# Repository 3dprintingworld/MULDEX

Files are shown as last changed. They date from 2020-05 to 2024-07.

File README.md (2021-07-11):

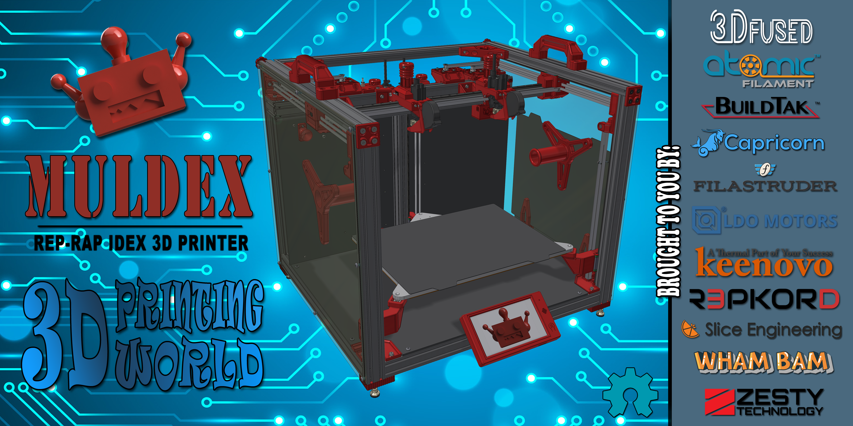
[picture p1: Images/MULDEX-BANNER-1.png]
Muldex


# Muldex
Opensource IDEX REP-RAP 3D Printer
### Print Volume:
Single Mode: 340mm x 300mm x 300mm<br/>
Copy Mode: 190mm x 300mm x 300mm<br/>
Dual Extruder: 310mm x 300mm x 300mm
### Build Platform:<br/>
300mm X 400mm <br/>
120v Silicone heater <br/>
8mm Mic 6 Aluminum Plate<br/>
Kinematic Coupled Bed<br/>
Independent motor leveled bed<br/>
Flex Plate System<br/>
### Kinematics:<br/>
X-Y-U Axis: Dual Markforged <br/>
Z-Axis: Belted 8mm Planetary Steppers<br/>
12 and 9mm Sq. Rail Bearings<br/>
Controller: Duet 2/Panel Due i7/Duex 5/Filament Monitors<br/>
Frame: 4020 & 2020 Extruded Aluminum<br/>
### Componets:<br/>
Independently Adjustable Nozzle Height - Slice Engineering Copperhead Hotend <br/>
Direct Drive Bondtech BMG Extruder or Remote Direct Drive Zesty Nimble Extruder <br/>
Purge Bucket/Ooze guards<br/>
Reverse Bowden w/filament runout<br/>
Bludex

### Links:
Facebook: [Muldex User Group](https://www.facebook.com/groups/961386687613469)<br/>
BMG Extruder Carriage Render: [Animation](https://https://youtu.be/zeYfmW2Gefs)<br/>
<br/>
Community Updates:<br/>
[ Guillaume's Drilling Jigs](https://www.prusaprinters.org/prints/32532-drilling-jigs-for-2020-and-2040-extrusions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)<br/>
[Guillame's Slim Fan Modules](https://www.prusaprinters.org/prints/57909-slim-fan-modules-for-muldex-3d-printer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)<br/>
[Guillame's Cable Duct](https://www.prusaprinters.org/prints/59193-industrial-style-cable-ducts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)<br/>
<br/>
### Kits from LDO are Available!!
Motor, rail, bolt, frame, and bed kits from LDO can be found [here](https://dddprintingworld.com/collections/mulex)<br/>
Custom cut Mic6 bed from [3Dfused ](https://3dfused.com/product/muldex-by-3dprinting-world-bed/)<br/>
Pannel Kit from [Repkord](https://www.repkord.com/products/sidepanel-set-for-muldex)<br/>
Additional links can be found in the bom. <br/>

### Sponsers:
[3D Fused](https://www.3dfused.com)<br/>
[Atomic Filament](https://www.atomicfilament.com)<br/>
[Buildtak](https://www.buildtak.com)<br/>
[Capricorn](https://www.captubes.com)<br/>
[Filastruder](https://www.filastruder.com)<br/>
[LDO Motors](https://www.ldomotors.com)<br/>
[Keenovo](https://keenovo.store/.com)<br/>
[Repkord](https://www.repkord.com)<br/>
[Slice Engineering](https://www.sliceengineering.com)<br/>
[Wham Bam](https://www.whambamsystems.com)<br/>
[Zesty Tech](https://zesty.tech/)<br/>

### Firmware, to do list:<br/>
1. Tool select Macros<br/>
2. Add macros to turn off mesh bed and change first layer heights<br/>
3. Mirror mode support<br/>

Note: current firmware only supports the BMG extruder, X-axis on left.<br/>
  
### Wiring
Wiring

### KINEMATICS
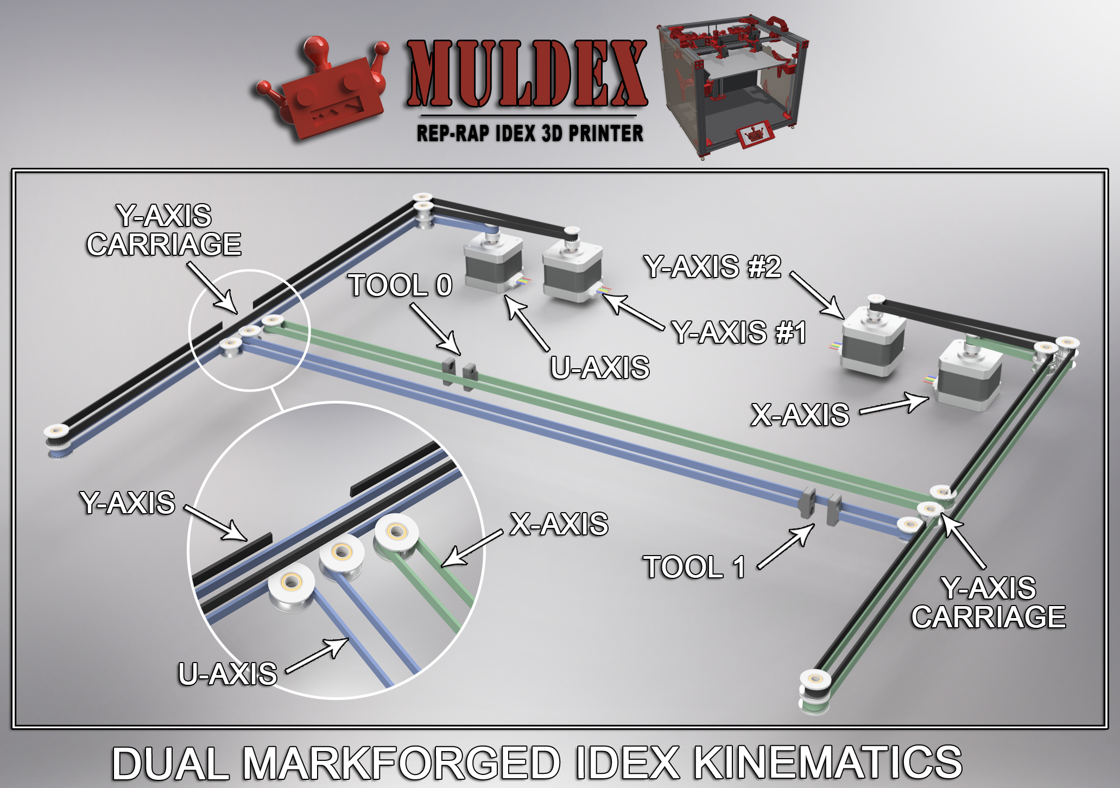
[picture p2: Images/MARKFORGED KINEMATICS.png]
Belt


### Print Examples
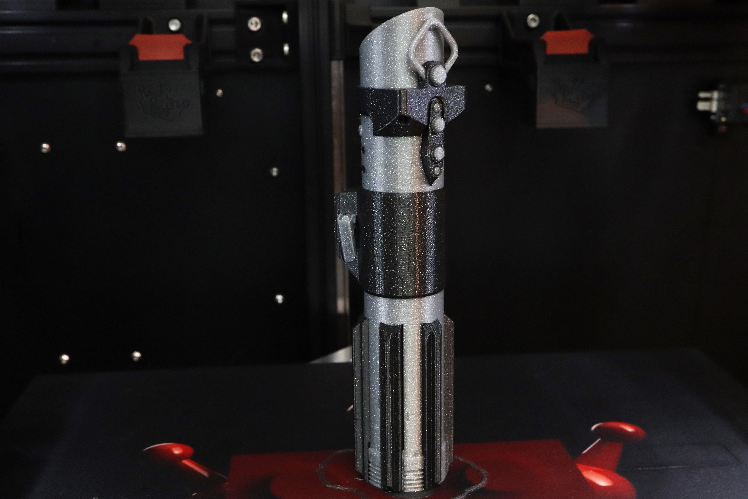
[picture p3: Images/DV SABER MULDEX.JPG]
Saber

Bull

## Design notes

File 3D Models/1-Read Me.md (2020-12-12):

Notice: Step files are prelimary and for reference only. For the most up to date models use the stl files.

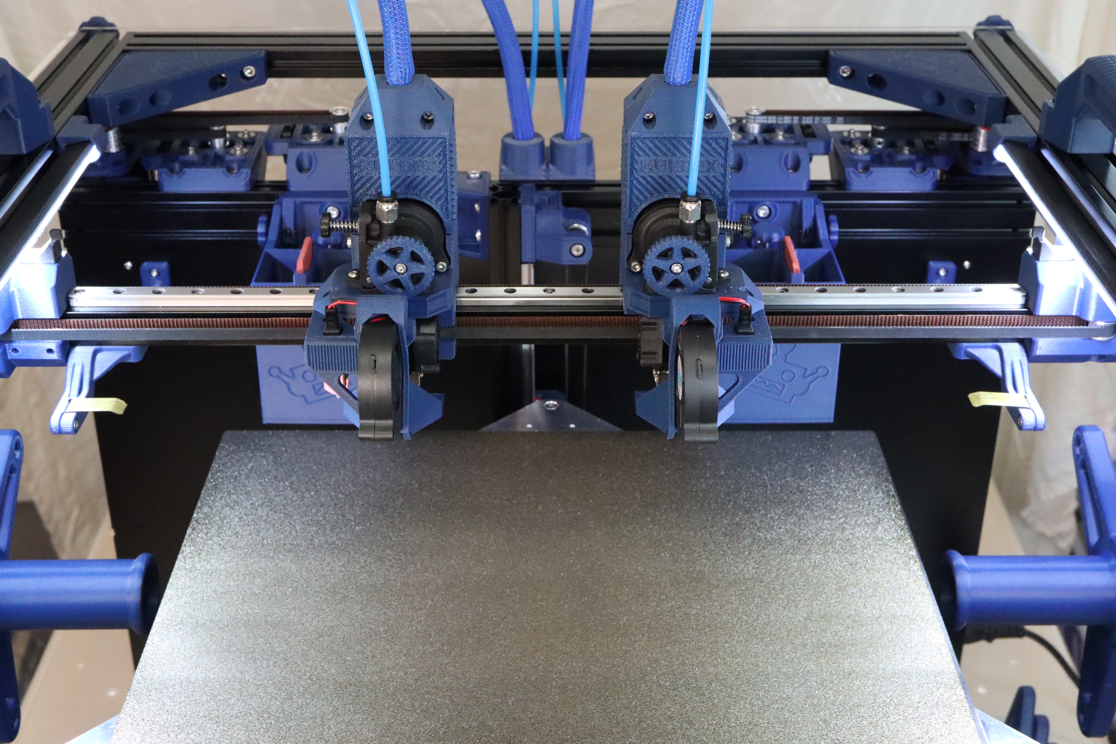
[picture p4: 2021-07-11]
Images/MULDEX-9.JPG

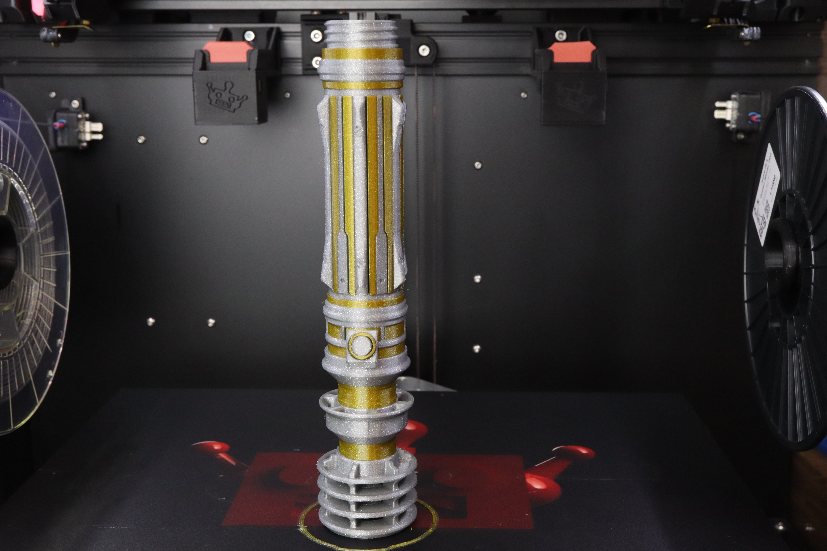
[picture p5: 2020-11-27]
Images/LEIA 1.JPG

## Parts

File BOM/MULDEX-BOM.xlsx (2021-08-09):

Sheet: COMPONENTS
2021-05-29 |  |  | BOM | TOTAL COST: | $2494.22 | (REF ONLY, CONTAINS OPTIONS)
QTY | Part Number | Description | Vendor | Thumbnail | UNIT | EACH | TOTAL | Notes:
1 | MULDEX-19-01 | BED PLATE | 3DFUSED (https://3dfused.com/product/muldex-by-3dprinting-world-bed/) |  | 1 | $135.00 | $135.00 | LDO ALTERATIVE (https://www.dddprintingworld.com/products/muldex-bed)
1 | MULDEX-11-02 | OOZE GUARD, X-AXIS | 3DPW |  |  |  | $0.00
1 | MULDEX-11-03 | OOZE GUARD, X-AXIS | 3DPW |  |  |  | $0.00
3 | 10MM X M4 | BALL END | ALIEXPRESS |  | 1 | $2.18 | $2.18
1 | 120C | THERMO FUSE | AMAZON (https://amzn.to/3wICdZ6) |  | 1 | $12.50 | $12.50
2 | JST-SM MALE | CONNECTOR | AMAZON (https://amzn.to/3oZNOjU) |  | 1 | $8.00 | $8.00
1 |  | WIRELESS MICROSCOPE | AMAZON (https://amzn.to/2XF4dyd) |  | 1 | $42.99 | $42.99 | OPTIONAL, FOR NOZZLE ALIGNMENT
3 | PETG | 1KG PETG CARBON FIBER | ATOMIC (https://atomicfilament.com/collections/petg-3d-printer-filament-us-made-with-free-shipping/products/carbon-fiber-black-petg-pro) |  | 3 | $49.99 | $149.97 | REQUIRES JUST OVER 2 KG
1 | BTFS300X400 | FLEX PLATE SYSTEM | BUILDTAK (https://www.buildtak.com/) |  | 1 | $140 | $140.00 | LDO POWER COATED ALTERATIVE $60.00 (https://www.dddprintingworld.com/products/powder-coated-pei-flex-plate)
2 | 1M LG | TL BOWDEN TUBING | CAPRICORN (https://www.captubes.com/shop/) |  | 2 | $11.99 | $23.98
2 | 4MM ID X 2MM ID 43.5MM LG | XS BOWDEN TUBING | CAPRICORN (https://www.captubes.com/shop/) |  | 1 | $11.99 | $11.99
1 | 5630 | LED STRIP W/EXTRUDED COVER 24V, DBL ROW | EBAY (https://www.ebay.com/itm/12V-24V-LED-5730-Strip-Light-Tube-Bar-Hard-Rigid-Lamp-White-For-Car-Showcase-USA/283971163922) |  | 2 | $3.81 | $7.62
16 | 5MM DIA X 3MM LG. | NEODYMIUM MAGNET | EBAY (https://www.ebay.com/itm/333227744234?var=542240236420) |  | 1 | $12.00 | $12.00
4 | 1.75 | E3D BOWDEN COUPLING, FOR PLASTIC | FILASTRUDER (https://www.filastruder.com/products/bowden-couplings-all-types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) |  | 2 | $2.99 | $5.98
4 | 2GT-16T-6-D | GATES DRIVE PULLEY, 16 TOOTH X 6MM WIDE | FILASTRUDER (https://www.filastruder.com/products/gates-2gt-pulley?_pos=1&_sid=b7f8e2fd2&_ss=r) |  | 4 | $4.99 | $19.96
10 | 2GT-20T-6-I | GATES IDLER PULLEY, 5MM BORE 20 TOOTH, 6MM WIDE | FILASTRUDER (https://www.filastruder.com/products/gates-2gt-idler?_pos=1&_sid=3b1905a2a&_ss=r) |  | 10 | $6.99 | $69.90
8 | 2GT-20T-6-SI | GATES IDLER PULLEY, 5MM BORE 20 SMOOTH, 6MM WIDE | FILASTRUDER (https://www.filastruder.com/products/gates-2gt-idler?_pos=1&_sid=3b1905a2a&_ss=r) |  | 8 | $7.49 | $59.92
3 | 2GT-20T-9-D | GATES DRIVE PULLEY, 20 TOOTH X 9MM WIDE | FILASTRUDER (https://www.filastruder.com/products/gates-2gt-pulley?_pos=1&_sid=b7f8e2fd2&_ss=r) |  | 3 | $5.99 | $17.97 | Requires the ID to be bored to 8mm. Consider Amazon or Aliexpress for 8mm bore. (https://amzn.to/3r480R3)
3 | 2GT-20T-9-I | GATES IDLER PULLEY, 5MM BORE 20 TOOTH, 9MM WIDE | FILASTRUDER (https://www.filastruder.com/products/gates-2gt-idler?_pos=1&_sid=3b1905a2a&_ss=r) |  | 3 | $6.99 | $20.97
18 | 5MM ID X 6MM OD X .4MM | BEARING SPACER | FILASTRUDER (https://www.filastruder.com/collections/railcore/products/shims-for-shoulder-screws?variant=17989593104455) |  | 1 | $9.99 | $9.99
2 | 6MM X 1290MM LG 2580 | GATES 2GT TIMING BELT | FILASTRUDER (https://www.filastruder.com/products/gates-2gt-belts?_pos=2&_sid=c064cd569&_ss=r) |  | 2 | $12.77 | $25.54
2 | 6MM X 2270MM LG | GATES 2GT TIMING BELT | FILASTRUDER (https://www.filastruder.com/products/gates-2gt-belts?_pos=2&_sid=c064cd569&_ss=r) |  | 2 | $22.47 | $44.94
1 | 7i | DUET 3D, PANELDUE | FILASTRUDER (https://www.filastruder.com/collections/electronics/products/paneldue-7i) |  | 1 | $99.99 | $99.99
3 | 9MM X 855MM LG. | GATES 2GT TIMING BELT | FILASTRUDER (https://www.filastruder.com/products/gates-2gt-belts?_pos=2&_sid=c064cd569&_ss=r) |  | 3 | $12.74 | $38.22
1 | AQA211VL | SSR | FILASTRUDER (https://www.filastruder.com/products/solid-state-relay?_pos=2&_sid=b83730b5f&_ss=r) |  | 1 | $21.99 | $21.99
1 | BL-TOUCH | LEVELING SENSOR | FILASTRUDER (https://www.filastruder.com/products/bltouch-automatic-bed-leveling-probe?_pos=4&_sid=87edbc376&_ss=r) |  | 1 | $34.99 | $34.99
1 | DUET 2 WIFI | DUET 3D, MAIN BOARD | FILASTRUDER (https://www.filastruder.com/collections/electronics/products/duet-wifi) |  | 1 | $169.99 | $169.99
1 | DUEX 5 | DUET 3D, EXPANSION BOARD | FILASTRUDER (https://www.filastruder.com/collections/electronics/products/duex2-and-duex-5-expansion-board) |  | 1 | $74.99 | $74.99
2 | FILAMENT SENSOR | DUET 3D, MAGNETIC TYPE | FILASTRUDER (https://www.filastruder.com/collections/electronics/products/duet-magnetic-filament-monitor) |  | 2 | $54.99 | $109.98 | OPTIONAL
3 | MGN12H x 370mm LG. G=10mm | LDO LINEAR RAIL, W/1 BEARING | FILASTRUDER (https://www.filastruder.com/products/ldo-linear-rails?variant=32433716265031) |  | 3 | $20.00 | $60.00 | INCLUDED IN LDO RAIL KIT
2 | MGN12H x 420mm lg. G=10mm | LDO LINEAR RAIL,, W/1 BEARING | FILASTRUDER (https://www.filastruder.com/products/ldo-linear-rails?variant=32433716265031) |  | 2 | $25.00 | $50.00 | INCLUDED IN LDO RAIL KIT
1 | MGN9H x 490mm lg. G=5mm | LDO LINEAR RAIL, W/2 BEARINGS | FILASTRUDER (https://www.filastruder.com/products/ldo-linear-rails?variant=32433716265031) |  | 1 | $35.00 | $35.00 | INCLUDED IN LDO RAIL KIT
1 | SM-DU-100 | BLTOUCH - 1 M CABLE | FILASTRUDER (https://www.filastruder.com/products/bltouch-1000mm-cable?_pos=1&_sid=87edbc376&_ss=r) |  | 1 | $2.99 | $2.99
1 | SILICONE | SILICONE HEATING PAD, 400X300 | KEENOVO (https://keenovo.store/products/keenovo-standard-rectangle-silicone-heater-3d-printer-build-plate-heatbed-heating-pad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) |  | 1 | $86.50 | $86.50
2 | 42STH25-1004AC | 1.8 SLIM POWER STEPPER | LDO (https://www.dddprintingworld.com/products/muldex-motor-kit) |  | 2 | $16 | $32.00 | INCLUDED IN LDO MOTOR KIT
4 | 42STH40-100AC | STEPPER MOTOR | LDO (https://www.dddprintingworld.com/products/muldex-motor-kit) |  | 4 | $16 | $64.00 | INCLUDED IN LDO MOTOR KIT
1 | LH-MIRRORED | ORBITER EXTRUDER | LDO (https://lukeslabonline.com/products/orbiter-v-1-5) |  | 1 | $55.00 | $55.00 | MJF PRINT MIRRORED HOUSING AND LEVERL
2 | OPTICAL | ENDSTOP SWITCH | HONG (https://www.amazon.com/gp/product/B071KBC3P8?linkId=593f3d3ddd48f557f777a21beb5f8118&language=en_US) |  | 1 | $9.96 | $9.96
1 | RH - STANDARD | ORBITER EXTRUDER | LDO (https://lukeslabonline.com/products/orbiter-v-1-5) |  | 1 | $55.00 | $55.00
1 | TOOL BOARD | DUMB BOARD, MULDEX ADDITION | LUKES LAB (https://lukeslabonline.com/products/dumbboard-muldex) |  | 2 | $15.00 | $30.00
3 | 1462N24 | SILICONE 1/8" X 3/4" CUT TO 1-3/4" LG. | MCMASTER (https://www.mcmaster.com/1462N24/) |  | 1 | $8.13 | $8.13 | OPTIONAL FOR WIPE
3 | 5862K124 | MAGNET, N52 1/2" DIA. X 3/8" THICK | MCMASTER (https://www.mcmaster.com/5862K124/) |  | 3 | $3.58 | $10.74
5 | 6301K780 | LEVELING FOOT, 6MM | MCMASTER (https://www.mcmaster.com/6301K78/) |  | 5 | $5.60 | $28.00 | OPTIONAL
4 | 92273A003 | GARLITE SPACER, .115"ID X .188" OD X.188" LG | MCMASTER (https://www.mcmaster.com/92273A003/) |  | 1 | $1.31 | $1.31 | OPTIONAL, BOWDEN TUBE WOULD ALSO WORK
1 | LRS-350-24 | MEANWELL POWER SUPPLY | MEANWELL (https://www.amazon.com/gp/product/B07SQLJG5L?linkId=c7ae342bb727b12a6109943f33807af6&language=en_US) |  | 1 | $32.20 | $32.20
2 | ZD-0026 | HORZONTAL LIMIT SWITCH | REIFENG (https://amzn.to/3cHwI2D) |  | 1 | $9.99 | $9.99 | OPTIONAL, ENDSTOPLESS HOMING FOR THE Y-AXIS
1 | MULDEX-00-01 | BACK COVER PANNEL | REPKORD (https://www.repkord.com/products/sidepanel-set-for-muldex) |  | 1 | $25.00 | $25.00
1 | MULDEX-03-03 | BACK PANNEL | REPKORD (https://www.repkord.com/products/sidepanel-set-for-muldex) |  | 1 | $25.00 | $25.00
1 | MULDEX-31-01 | SIDE PANEL | REPKORD (https://www.repkord.com/products/sidepanel-set-for-muldex) |  | 1 | $25.00 | $25.00
1 | MULDEX-31-02 | SIDE PANEL, IEC | REPKORD (https://www.repkord.com/products/sidepanel-set-for-muldex) |  | 1 | $25.00 | $25.00
1 | MULDEX-32-01 | BOTTOM PANNEL | REPKORD (https://www.repkord.com/products/sidepanel-set-for-muldex) |  | 1 | $25.00 | $25.00
1 | 4304.6072 | IEC INLET C14 W/SWITCH | SCHURTER (https://www.digikey.com/en/products/detail/schurter-inc/4304-6072/2645660) |  | 1 | $9.00 | $9.00
2 | .4MM | VANADUM NOZZLE | SLICE (https://www.sliceengineering.com/products/copperhead%E2%84%A2) |  | 2 | $34.99 | $69.98
2 | 25X25X10 | 24V DC FAN | SLICE (https://www.sliceengineering.com/products/copperhead%E2%84%A2) |  | 2 | $6.99 | $13.98
2 | COPPERHEAD-1 | HEAT BREAK, STANDARD VARIANT | SLICE (https://www.sliceengineering.com/products/copperhead%E2%84%A2) |  | 2 | $29.99 | $59.98
2 | COPPERHEAD-2 | HOT BLOCK | SLICE (https://www.sliceengineering.com/products/copperhead%E2%84%A2) |  | 2 | $24.99 | $49.98
2 | COPPERHEAD-3 | HEAT SINK,SCREW MOUNT | SLICE (https://www.sliceengineering.com/products/copperhead%E2%84%A2) |  | 2 | $44.99 | $89.98
2 | COPPERHEAD-4 | HIGH TEMP THERMISTER | SLICE (https://www.sliceengineering.com/collections/accessories/products/thermistor-high-temperature) |  | 2 | $39.99 | $79.98
2 | COPPERHEAD-5 | 24V, HEATER CARTRIAGE | SLICE (https://www.sliceengineering.com/collections/accessories/products/50w-heater-cartridge?variant=29760199196744) |  | 2 | $19.99 | $39.98
2 | 5015 | BLOWER, 24VDC | SOUND ORIGINAL (https://amzn.to/2XFXwvH) |  | 1 | $13.99 | $13.99
1 | MULDEX-19-03 | FLEX PLATE | WHAM BAM |  |  |  | $0.00

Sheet: EXTRUSIONS
2021-05-29 |  |  | BOM | TOTAL COST: | $184.00 | (REF ONLY, CONTAINS OPTIONS)
QTY | Part Number | Description | Vendor | Thumbnail | UNIT | EACH | TOTAL | Notes:
1 | MULDEX-01-09 | EXTRUSION, Z-AXIS | LDO (https://www.dddprintingworld.com/products/ldo-frame-kit) |  | 1 | $7.00 | $7.00 | ALTERATIVE MISUMI PN: HFSB5-2040-455 INCLUDED IN LDO FRAME KIT
1 | MULDEX-01-10 | EXTRUSION, MOTOR MOUNT | LDO (https://www.dddprintingworld.com/products/ldo-frame-kit) |  | 1 | $9.00 | $9.00 | ALTERATIVE MISUMI PN: HFSB5-2040-635
2 | MULDEX-02-01 | EXTRUSIOIN, Y-AXIS | LDO (https://www.dddprintingworld.com/products/ldo-frame-kit) |  | 2 | $9.00 | $18.00 | ALTERATIVE MISUMI PN: HFSB5-2040-555 INCLUDED IN LDO FRAME KIT
2 | MULDEX-02-02 | EXTRUSION, STANDOFF | LDO (https://www.dddprintingworld.com/products/fastener-kit) |  | 2 | $6.00 | $12.00 | ALTERATIVE MISUMI PN: HFSB5-2040-60-SC INCLUDED IN LDO FRAME KIT
2 | MULDEX-02-03 | EXTRUSION, FRONT VERTICAL | LDO (https://www.dddprintingworld.com/products/ldo-frame-kit) |  | 2 | $12.00 | $24.00 | ALTERATIVE MISUMI PN: HFSB5-2040-505-SC INCLUDED IN LDO FRAME KIT
2 | MULDEX-02-04 | EXTRUSION, BACK VERTICAL | LDO (https://www.dddprintingworld.com/products/ldo-frame-kit) |  | 2 | $15.00 | $30.00 | ALTERATIVE MISUMI PN: HFSB5-2040-505-SC INCLUDED IN LDO FRAME KIT
1 | MULDEX-02-05 | EXTRUSION, BACK SUPPORT | LDO (https://www.dddprintingworld.com/products/ldo-frame-kit) |  | 1 | $12.00 | $12.00 | ALTERATIVE MISUMI PN: HFSB5-2020-555-SC INCLUDED IN LDO FRAME KIT
2 | MULDEX-02-06 | EXTRUSION, FRONT BOTTOM | LDO (https://www.dddprintingworld.com/products/ldo-frame-kit) |  | 2 | $14.00 | $28.00 | ALTERATIVE MISUMI PN: HFSB5-2040-555-SC INCLUDED IN LDO FRAME KIT
2 | MULDEX-02-07 | EXTRUSION, BOTTOM SIDES | LDO (https://www.dddprintingworld.com/products/ldo-frame-kit) |  | 2 | $14.00 | $28.00 | ALTERATIVE MISUMI PN: HFSB5-2040-515-SC INCLUDED IN LDO FRAME KIT
1 | MULDEX-02-08 | EXTRUSION, BACK | LDO (https://www.dddprintingworld.com/products/ldo-frame-kit) |  | 1 | $16.00 | $16.00 | ALTERATIVE MISUMI PN: HFSB5-2040-595-SC INCLUDED IN LDO FRAME KIT

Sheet: FASTENERS
2021-05-29 |  |  | BOM | TOTAL COST: | $88.69 | (REF ONLY, CONTAINS OPTIONS)
QTY | Part Number | Description | Vendor | Thumbnail | UNIT | EACH | TOTAL | Notes:
2 | M4x0.7 x 35 | SHCS |  |  | 1 |  | $0.00 | INCLUDED IN LDO FASTENER KIT
4 | M2.5x0.45 x 10 | SHCS |  |  | 1 |  | $0.00 | INCLUDED IN LDO FASTENER KIT
4 | M2.5x0.45 x 12 | SHCS |  |  | 1 |  | $0.00 | INCLUDED IN LDO FASTENER KIT
16 | M3 | WASHER |  |  | 1 |  | $0.00 | INCLUDED IN LDO FASTENER KIT
50 | M3 x 0.5 | Hex Nut |  |  | 1 |  | $0.00 | INCLUDED IN LDO FASTENER KIT
17 | M3 x 0.5 x 10 | BHCS | https://www.dddprintingworld.com/products/fastener-kit |  | 1 |  | $0.00 | INCLUDED IN LDO FASTENER KIT
4 | M3 x 0.5 x 16 | BHCS |  |  | 1 |  | $0.00 | INCLUDED IN LDO FASTENER KIT
6 | M3 x 0.5 x 20 | HHCS |  |  | 1 |  | $0.00 | INCLUDED IN LDO FASTENER KIT
35 | M3x0.5 x 10 | SHCS |  |  | 1 |  | $0.00 | INCLUDED IN LDO FASTENER KIT
30 | M3x0.5 x 12 | SHCS |  |  | 1 |  | $0.00 | INCLUDED IN LDO FASTENER KIT
31 | M3x0.5 x 16 | SHCS |  |  | 1 |  | $0.00 | INCLUDED IN LDO FASTENER KIT
10 | M3x0.5 x 20 | SHCS |  |  | 1 |  | $0.00 | INCLUDED IN LDO FASTENER KIT
8 | M3x0.5 x 25 | SHCS |  |  | 1 |  | $0.00 | INCLUDED IN LDO FASTENER KIT
2 | M3x0.5 x 30 | SHCS |  |  | 1 |  | $0.00 | INCLUDED IN LDO FASTENER KIT
8 | M3x0.5 x 6 | SHCS |  |  | 1 |  | $0.00 | INCLUDED IN LDO FASTENER KIT
63 | M3x0.5 x 8 | SHCS |  |  | 1 |  | $0.00 | INCLUDED IN LDO FASTENER KIT
8 | M4 | Square Nut |  |  | 1 |  | $0.00 | INCLUDED IN LDO FASTENER KIT
16 | M4 x 0.7 | Hex Nut |  |  | 1 |  | $0.00 | INCLUDED IN LDO FASTENER KIT
10 | M4 x 0.7 x 12 | BHCS |  |  | 1 |  | $0.00 | INCLUDED IN LDO FASTENER KIT
4 | M4 x 0.7 x 8 | BHCS |  |  | 1 |  | $0.00 | INCLUDED IN LDO FASTENER KIT
3 | M4x12 | FHCS |  |  | 1 |  | $0.00 | INCLUDED IN LDO FASTENER KIT
6 | M5 x 0.8 | Hex Nut |  |  | 1 |  | $0.00 | INCLUDED IN LDO FASTENER KIT
22 | M5 x 0.8 x 10 | BHCS |  |  | 1 |  | $0.00 | INCLUDED IN LDO FASTENER KIT
2 | M5 x 0.8 x 16 | HHCS |  |  | 1 |  | $0.00 | INCLUDED IN LDO FASTENER KIT
6 | M5 x 0.8 x 16 | BHCS |  |  | 1 |  | $0.00 | INCLUDED IN LDO FASTENER KIT
43 | M5 x 0.8 x 8 | BHCS |  |  | 1 |  | $0.00 | INCLUDED IN LDO FASTENER KIT
75 | M5x0.8 x 10 | SHCS |  |  | 1 |  | $0.00 | INCLUDED IN LDO FASTENER KIT
12 | M5x0.8 x 12 | SHCS |  |  | 1 |  | $0.00 | INCLUDED IN LDO FASTENER KIT
52 | M5x0.8 x 16 | SHCS |  |  | 1 |  | $0.00 | INCLUDED IN LDO FASTENER KIT
19 | M5x0.8 x 20 | SHCS |  |  | 1 |  | $0.00 | INCLUDED IN LDO FASTENER KIT
2 | M5x0.8 x 25 | SHCS |  |  | 1 |  | $0.00 | INCLUDED IN LDO FASTENER KIT
8 | M5x12 | FHCS |  |  | 1 |  | $0.00 | INCLUDED IN LDO FASTENER KIT
51 | M3-20 SERIES | T-NUT, TWIST LOCK | AMAZON (https://amzn.to/2AKpMVb) |  | 1 |  | $0.00 | INCLUDED IN LDO FASTENER KIT
181 | M5-20 SERIES | T-NUT, TWIST LOCK | AMAZON (https://amzn.to/3gYKykv) |  | 2 |  | $0.00 | INCLUDED IN LDO FASTENER KIT
9 | M5 X 25MM LG. | S.S. SHOULDER BOLT | FILASTRUDER (https://www.filastruder.com/products/shoulder-screws-bolts?_pos=1&_sid=c289bef45&_ss=r&variant=17989593104455) |  | 9 | $1.99 | $17.91
6 | M5 X 30MM LG. | S.S. SHOULDER BOLT | FILASTRUDER (https://www.filastruder.com/products/shoulder-screws-bolts?_pos=1&_sid=c289bef45&_ss=r&variant=17989593104455) |  | 6 | $1.99 | $11.94
1 | FASTENER KIT | THE FASTERNERS MARKED INCLUDED IN THE NOTES COLUMN | LDO (https://www.dddprintingworld.com/products/fastener-kit) |  | 1 | $42.00 | $42.00
2 | 93625A100 | M3 NYLOCK | MCMASTER |  | 1 | $5.31 | $5.31 | OPTIONAL, STANDARD NUT WOULD WORK
5 | 94180A371 | HEAT SET INSERT, M6 | MCMASTER (https://www.mcmaster.com/catalog/126/3507) |  | 1 | 9.68 | $9.68 | OPTIONAL, FOR MOUNTING FOOT
41 | IUB-M3-1 | M3 HEAT SET INSERT, MINI | PEM (https://www.dddprintingworld.com/products/fastener-kit) |  | 41 | $0.04 | $1.84

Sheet: ASSEMBLIES
2021-05-29 |  |  | BOM | TOTAL COST: | $0.00 | (REF ONLY, CONTAINS OPTIONS)
QTY | Part Number | Description | Vendor | Thumbnail | UNIT | EACH | TOTAL | Notes:
1 | MULDEX-01 | FRAME ASSEMBLY | 3DPW |  |  |  | $0.00
1 | MULDEX-02 | FRAME SUB-ASSEMBLY | 3DPW |  |  |  | $0.00
1 | MULDEX-03 | BACK PANEL ASSEMBLY | 3DPW |  |  |  | $0.00
1 | MULDEX-04 | MNT FOOT, FRONT LEFT | 3DPW |  |  |  | $0.00
1 | MULDEX-05 | MNT FOOT, FRONT RIGHT | 3DPW |  |  |  | $0.00
1 | MULDEX-06 | MNT FOOT, BACK RIGHT | 3DPW |  |  |  | $0.00
1 | MULDEX-07 | MOUNTING FOOT, BACK LEFT | 3DPW |  |  |  | $0.00
1 | MULDEX-08 | MOUNTING FOOT, CENTER | 3DPW |  |  |  | $0.00
1 | MULDEX-10 | KINEMATIC ASSEMBLY | 3DPW |  |  |  | $0.00
1 | MULDEX-11 | X-AXIS ASSEMBLY | 3DPW |  |  |  | $0.00
1 | MULDEX-43 | X-AXIS CARRIAGE | 3DPW |  |  |  | $0.00
1 | MULDEX-44 | U-AXIS CARRIAGE | 3DPW |  |  |  | $0.00
2 | MULDEX-14 | Y-AXIS CARRIAGE | 3DPW |  |  |  | $0.00
1 | MULDEX-15 | Z-AXIS ASSEMBLY | 3DPW |  |  |  | $0.00
1 | MULDEX-16 | Z-AXIS BELT ASSY, 1 | 3DPW |  |  |  | $0.00
1 | MULDEX-17 | Z-AXIS BELT ASSY, 2 | 3DPW |  |  |  | $0.00
1 | MULDEX-18 | Z-AXIS BELT ASSY, 3 | 3DPW |  |  |  | $0.00
1 | MULDEX-19 | HEAT BED ASSEMBLY | 3DPW |  |  |  | $0.00
1 | MULDEX-20 | IDLE ASSEMBLY, LH | 3DPW |  |  |  | $0.00
1 | MULDEX-21 | IDLE ASSEMBLY, LH | 3DPW |  |  |  | $0.00
1 | MULDEX-22 | U-AXIS MOTOR ASSY | 3DPW |  |  |  | $0.00
1 | MULDEX-23 | X-AXIS MOTOR ASSY | 3DPW |  |  |  | $0.00
1 | MULDEX-24 | Y-AXIS MOTOR ASSY, LH | 3DPW |  |  |  | $0.00
1 | MULDEX-25 | Y-AXIS MOTOR ASSY, RH | 3DPW |  |  |  | $0.00
2 | MULDEX-27 | THUMB SCREW ASSEMBLY | 3DPW |  |  |  | $0.00
1 | MULDEX-28 | FLEX PLATE CADDY ASSY | 3DPW |  |  |  | $0.00
2 | MULDEX-29 | BOWDEN STRAIN RELIF ASSY | 3DPW |  |  |  | $0.00
1 | MULDEX-30 | PANNEL ASSY, LEFT | 3DPW |  |  |  | $0.00
1 | MULDEX-31 | PANNEL ASSEMBLY, RIGHT | 3DPW |  |  |  | $0.00
1 | MULDEX-32 | BOTTOM PANEL ASSY | 3DPW |  |  |  | $0.00
1 | MULDEX-33 | SCRAPER ASSEMBLY, U-AXIS | 3DPW |  |  |  | $0.00
1 | MULDEX-34 | SCRAPPER ASSY, X-AXIS | 3DPW |  |  |  | $0.00
1 | MULDEX-35 | DUET PANNEL | 3DPW |  |  |  | $0.00
2 | MULDEX-36 | LIGHT BAR ASSEMBLY | 3DPW |  |  |  | $0.00
1 | MULDEX-37 | Y-AXIS STOP, RH | 3DPW |  |  |  | $0.00
1 | MULDEX-38 | Y-AXIS STOP, LH | 3DPW |  |  |  | $0.00
1 | MULDEX-41 | IEC CONNECTOR ASSY - UL | 3DPW |  |  |  | $0.00

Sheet: PRINTED PARTS
2021-05-29 |  |  | BOM | TOTAL COST: | $0.00 | (REF ONLY, CONTAINS OPTIONS)
QTY | Part Number | Description | Vendor | Thumbnail | UNIT | EACH | TOTAL | Notes:
2 | MULDEX-11-09 | SWITCH TRIGGER | ATOMIC |  | 1 |  | $0.00
1 | MULBOT-34-01 | SCRAPPER, FRAME X-AXIS | ATOMIC |  | 1 |  | $0.00
2 | MULDEX-01-01 | FRAME CORNER GUSSET | ATOMIC |  | 1 |  | $0.00
8 | MULDEX-01-02 | BACK PLATE BRACKET | ATOMIC |  | 1 |  | $0.00
2 | MULDEX-01-03 | PANNEL SUPPORT | ATOMIC |  | 1 |  | $0.00
1 | MULDEX-01-04 | Z-AXIS RAIL SUPPORT | ATOMIC |  | 1 |  | $0.00
2 | MULDEX-01-05 | HANDLE | ATOMIC |  | 1 |  | $0.00
2 | MULDEX-01-06 | FRONT END CAP | ATOMIC |  | 1 |  | $0.00
1 | MULDEX-01-07 | ENDCAP COVER | ATOMIC |  | 1 |  | $0.00
1 | MULDEX-03-01 | BACK PLATE, STRAIN RELIF | ATOMIC |  | 1 |  | $0.00
2 | MULDEX-03-02 | SENSOR MOUNT | ATOMIC |  | 1 |  | $0.00 | Optional- for filament monitor
8 | MULDEX-03-04 | DUET SPACER | ATOMIC |  | 1 |  | $0.00
3 | MULDEX-03-05 | INLET GUIDE | ATOMIC |  | 1 |  | $0.00 | Optional-If no filament monitor
2 | MULDEX-03-06 | CABLE COVER, STRAIGHT | ATOMIC |  | 1 |  | $0.00
2 | MULDEX-03-07 | CABLE COVER, VERT SHORT | ATOMIC |  | 1 |  | $0.00
2 | MULDEX-03-08 | CABLE COVER, HORZ | ATOMIC |  | 1 |  | $0.00
1 | MULDEX-03-08 | WIRE CLIP | ATOMIC |  | 1 |  | $0.00
2 | MULDEX-03-09 | CABLE COVER, VERT LONG | ATOMIC |  | 1 |  | $0.00
1 | MULDEX-03-10 | CABLE DUCT, BOTTOM | ATOMIC |  | 1 |  | $0.00
1 | MULDEX-03-11 | CABLE DUCT, TOP | ATOMIC |  | 1 |  | $0.00
1 | MULDEX-03-12 | CABLE DUCT, STRAIGHT | ATOMIC |  | 1 |  | $0.00
1 | MULDEX-03-13 | BACK PLATE, STRAIN RELIEF | ATOMIC |  | 1 |  | $0.00
1 | MULDEX-04-01 | FOOT PAD, FRONT LEFT | ATOMIC |  | 1 |  | $0.00
1 | MULDEX-05-01 | FOOT PAD, FRONT RIGHT | ATOMIC |  | 1 |  | $0.00
1 | MULDEX-06-01 | FOOT PAD, BACK RIGHT | ATOMIC |  | 1 |  | $0.00
1 | MULDEX-07-01 | FOOT PAD, BACK LEFT | ATOMIC |  | 1 |  | $0.00
1 | MULDEX-08-01 | FOOT PAD, CENTER | ATOMIC |  | 1 |  | $0.00
1 | MULDEX-11-06 | OOZE BLOCK, RH | ATOMIC |  | 1 |  | $0.00 | OPTIONAL
1 | MULDEX-11-07 | OOZE BLOCK, LH | ATOMIC |  | 1 |  | $0.00 | OPTIONAL
4 | MULDEX-12-02 | BELT CLAMP | ATOMIC |  | 1 |  | $0.00
2 | MULDEX-14-01 | Y-AXIS, BASE BLOCK | ATOMIC |  | 1 |  | $0.00
2 | MULDEX-14-02 | Y-AXIS, CLAMP BLOCK | ATOMIC |  | 1 |  | $0.00
2 | MULDEX-14-03 | Y-AXIS BELT CLAMP | ATOMIC |  | 1 |  | $0.00
2 | MULDEX-16-01 | Z-AXIS MOTOR MOUNT, 1&3 | ATOMIC |  | 1 |  | $0.00
1 | MULDEX-16-02 | Z-AXIS COUPLING, 1 | ATOMIC |  | 1 |  | $0.00
1 | MULDEX-16-03 | Z-AXIS TAKEUP MOUNT, 1 | ATOMIC |  | 1 |  | $0.00
1 | MULDEX-16-04 | Z-AXIS TAKUP BRACKET, 1 | ATOMIC |  | 1 |  | $0.00
3 | MULDEX-16-05 | BELT CLAMP, Z | ATOMIC |  | 1 |  | $0.00
3 | MULDEX-16-06 | BELT CLAMP, Z | ATOMIC |  | 1 |  | $0.00
1 | MULDEX-17-02 | Z-AXIS TAKUP, 2 | ATOMIC |  | 1 |  | $0.00
1 | MULDEX-17-03 | Z-AXIS COUPLING, 2 | ATOMIC |  | 1 |  | $0.00
1 | MULDEX-17-04 | Z-AXIS MOTOR MOUNT, 2 | ATOMIC |  | 1 |  | $0.00
1 | MULDEX-17-05 | Z-AXIS TAKUP MOUNT, 2 | ATOMIC |  | 1 |  | $0.00
1 | MULDEX-18-02 | Z-AXIS COUPLING, 3 | ATOMIC |  | 1 |  | $0.00
1 | MULDEX-18-03 | Z-AXIS TAKUP MOUNT, 3 | ATOMIC |  | 1 |  | $0.00
1 | MULDEX-18-04 | Z-AXIS TAKEUP, 2 | ATOMIC |  | 1 |  | $0.00
1 | MULDEX-19-04 | STRAIN RELIEF | ATOMIC |  | 1 |  | $0.00
1 | MULDEX-20-01 | CORNER IDLER, RH | ATOMIC |  | 1 |  | $0.00
1 | MULDEX-21-01 | CORNER IDLER, LH | ATOMIC |  | 1 |  | $0.00
1 | MULDEX-22-01 | U-AXIS STEPPER MOUNT | ATOMIC |  | 1 |  | $0.00
4 | MULDEX-22-02 | TAKE UP KNOB | ATOMIC |  | 1 |  | $0.00
1 | MULDEX-23-01 | X-AXIS STEPPER MOUNT | ATOMIC |  | 1 |  | $0.00
1 | MULDEX-24-01 | Y-AXIS MOTOR MOUNT, LH | ATOMIC |  | 1 |  | $0.00
1 | MULDEX-25-01 | Y-AXIS MOTOR MOUNT, RH | ATOMIC |  | 1 |  | $0.00
2 | MULDEX-27-01 | THUMB KNOB, M5 HEX | ATOMIC |  | 1 |  | $0.00
2 | MULDEX-27-02 | THUMB KNOB COVER | ATOMIC |  | 1 |  | $0.00
2 | MULDEX-28-01 | FLEX PLATE CADDY | ATOMIC |  | 1 |  | $0.00 | OPTIONAL
2 | MULDEX-29-01 | REVERSE BOWDEN BRACKET | ATOMIC |  | 1 |  | $0.00
2 | MULDEX-29-03 | EXTRUDER CABLE, CLAMP | ATOMIC |  | 1 |  | $0.00
2 | MULDEX-29-04 | WIRE COMB | ATOMIC |  | 1 |  | $0.00
2 | MULDEX-30-02 | SPOOL HOLDER | ATOMIC |  | 1 |  | $0.00
1 | MULDEX-32-02 | FRONT BELT COVER, LH | ATOMIC |  | 1 |  | $0.00
1 | MULDEX-32-03 | FRONT BELT COVER, RH | ATOMIC |  | 1 |  | $0.00
1 | MULDEX-32-04 | BACK BELT COVER | ATOMIC |  | 1 |  | $0.00
1 | MULDEX-33-01 | SCRAPPER, FRAME U-AXIS | ATOMIC |  | 1 |  | $0.00 | OPTIONAL
2 | MULDEX-33-02 | PURGE BIN | ATOMIC |  | 1 |  | $0.00 | OPTIONAL
2 | MULDEX-33-03 | SCRAPPER BASE | ATOMIC |  | 1 |  | $0.00 | OPTIONAL
2 | MULDEX-33-04 | SCRAPER KNOB | ATOMIC |  | 1 |  | $0.00 | OPTIONAL
1 | MULDEX-35-01 | PANEL, BEZEL | ATOMIC |  | 1 |  | $0.00
1 | MULDEX-35-02 | PANEL, BACK PLATE | ATOMIC |  | 1 |  | $0.00
2 | MULDEX-35-03 | PANEL, BASE BRACKET | ATOMIC |  | 1 |  | $0.00
1 | MULDEX-35-04 | PANEL, MOUNTING CLEVIS | ATOMIC |  | 1 |  | $0.00
1 | MULDEX-36-01 | LIGHT END BRACKET, RH | ATOMIC |  | 1 |  | $0.00
1 | MULDEX-36-02 | LIGHT END BRACKET, LH | ATOMIC |  | 1 |  | $0.00
1 | MULDEX-37-01 | Y STOP BRACKET, RH | ATOMIC |  | 1 |  | $0.00 | OPTIONAL
1 | MULDEX-38-01 | Y STOP BRACKET, RH | ATOMIC |  | 1 |  | $0.00 | OPTIONAL
1 | MULDEX-41-01 | IEC SOCET COVER- UL | ATOMIC |  | 1 |  | $0.00
1 | MULDEX-41-02 | IEC SOCKET BASE - UL | ATOMIC |  | 1 |  | $0.00
1 | MULDEX-43-01 | X-AXIS, SCREW MOUNT | ATOMIC |  | 1 |  | $0.00
1 | MULDEX-43-02 | X-AXIS FRONT COVER | ATOMIC |  | 1 |  | $0.00
1 | MULDEX-43-03 | X-AXIS, CARRIAGE ORBITER | ATOMIC |  | 1 |  | $0.00
1 | MULDEX-43-04 | X-AXIS COOLING SHROUD | ATOMIC |  | 1 |  | $0.00
2 | MULDEX-43-05 | FEED LEVER | ATOMIC |  | 1 |  | $0.00 | OPTIONAL
1 | MULDEX-44-01 | U-AXIS, CARRIAGE ORBITER | ATOMIC |  | 1 |  | $0.00
1 | MULDEX-44-02 | U-AXIS, GROOVE MOUNT | ATOMIC |  | 1 |  | $0.00
1 | MULDEX-44-03 | U-AXIS BACK COVER | ATOMIC |  | 1 |  | $0.00
1 | MULDEX-44-04 | U-COOLING SHROUD | ATOMIC |  | 1 |  | $0.00

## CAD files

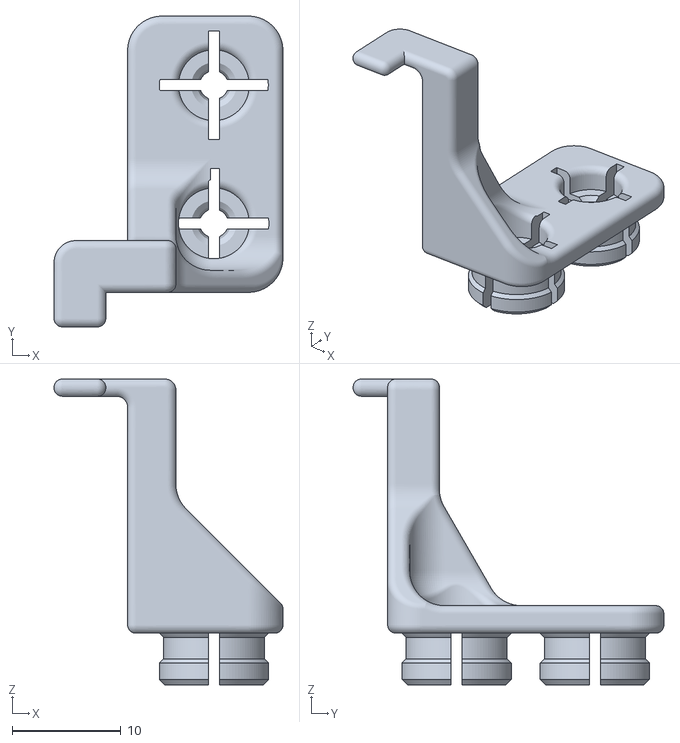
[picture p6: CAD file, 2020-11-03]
3D Models/BMG/MULDEX-39-05.stl
21.1 x 28.6 x 28.1

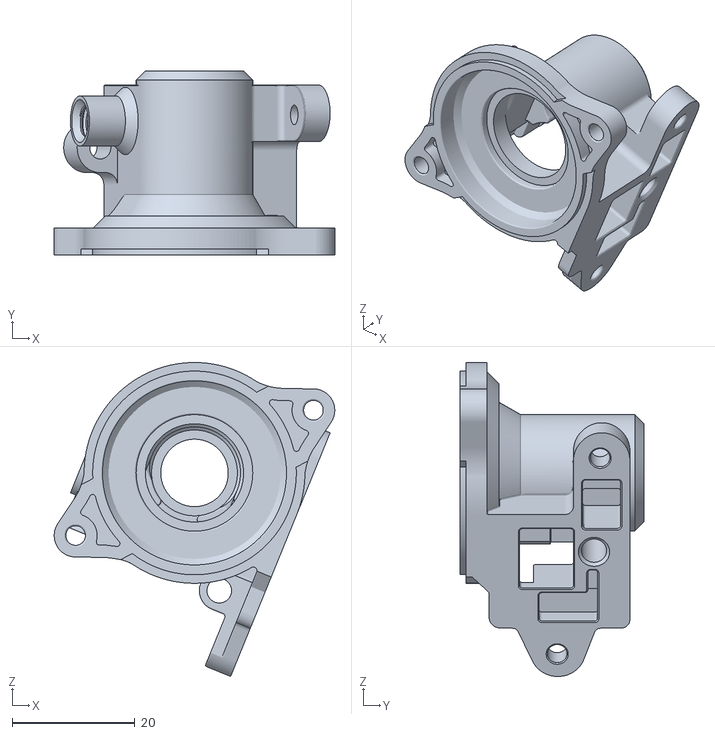
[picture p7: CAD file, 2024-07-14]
3D Models/MIRRORED ORBITER/Housing 1.5_mirrored.stl
45.7 x 30.0 x 51.2

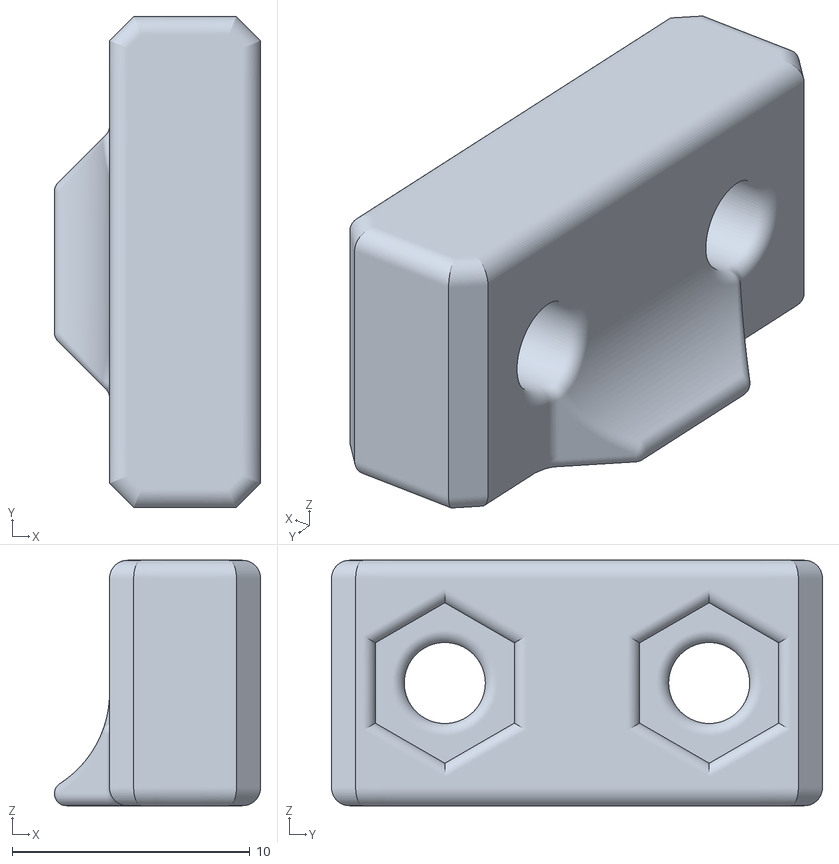
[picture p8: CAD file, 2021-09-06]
3D Models/MULDEX-12-02.stl
8.67 x 20.6 x 10.3

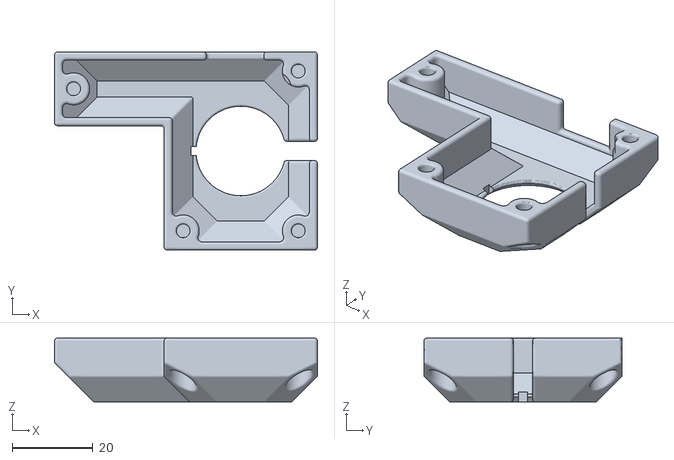
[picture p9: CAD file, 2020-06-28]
3D Models/Nimble/MULDEX-12-05.stl
65.3 x 49.2 x 15.9

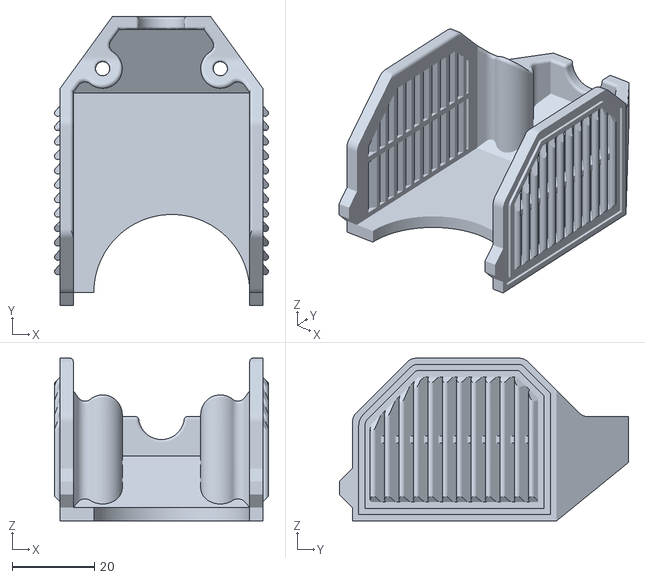
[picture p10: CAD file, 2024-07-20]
3D Models/Orbiter V2/MULDEX-50-04.stl
52.0 x 70.2 x 39.5

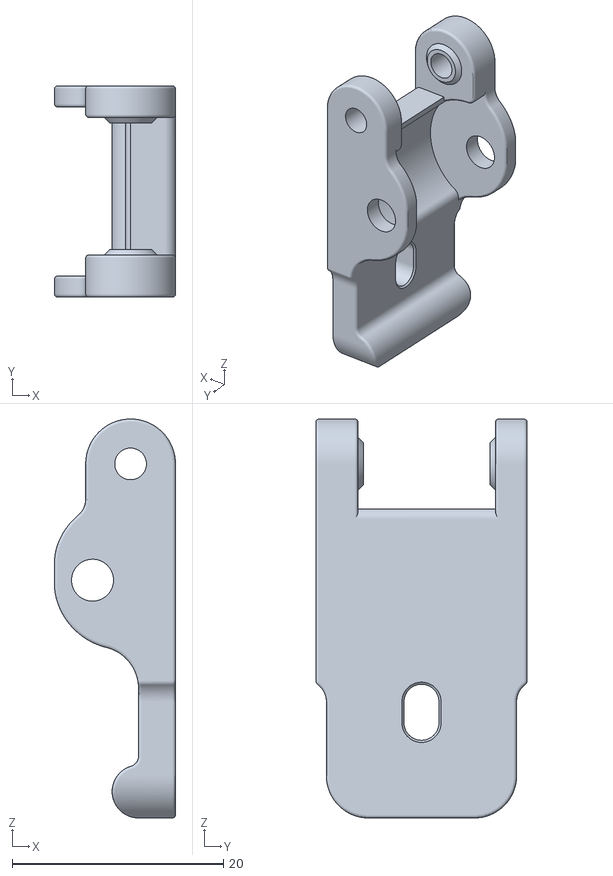
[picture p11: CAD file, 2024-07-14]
3D Models/MIRRORED ORBITER/Latch_mirrored.stl
11.4 x 20.0 x 37.7

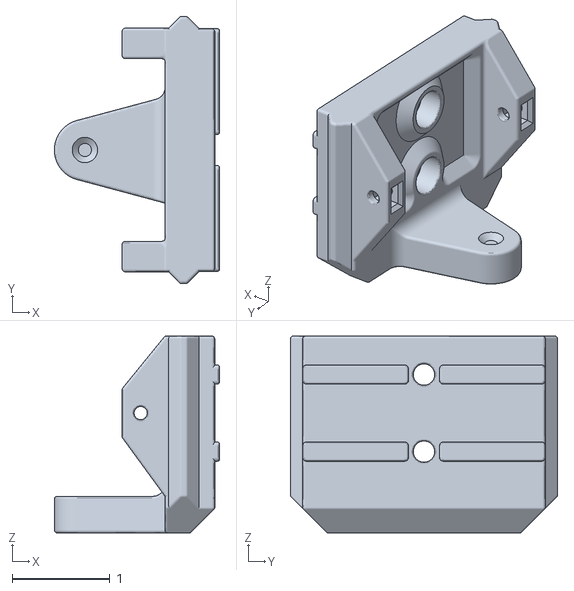
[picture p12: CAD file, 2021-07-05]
3D Models/MULDEX-33-03.stl
1.69 x 2.73 x 2.01

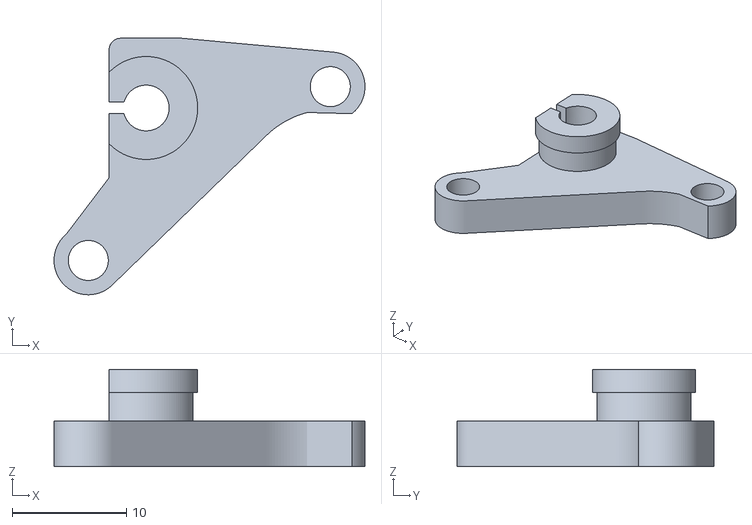
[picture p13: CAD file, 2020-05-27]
3D Models/Nimble/MULDEX-12-04.stl
27.2 x 22.4 x 8.50

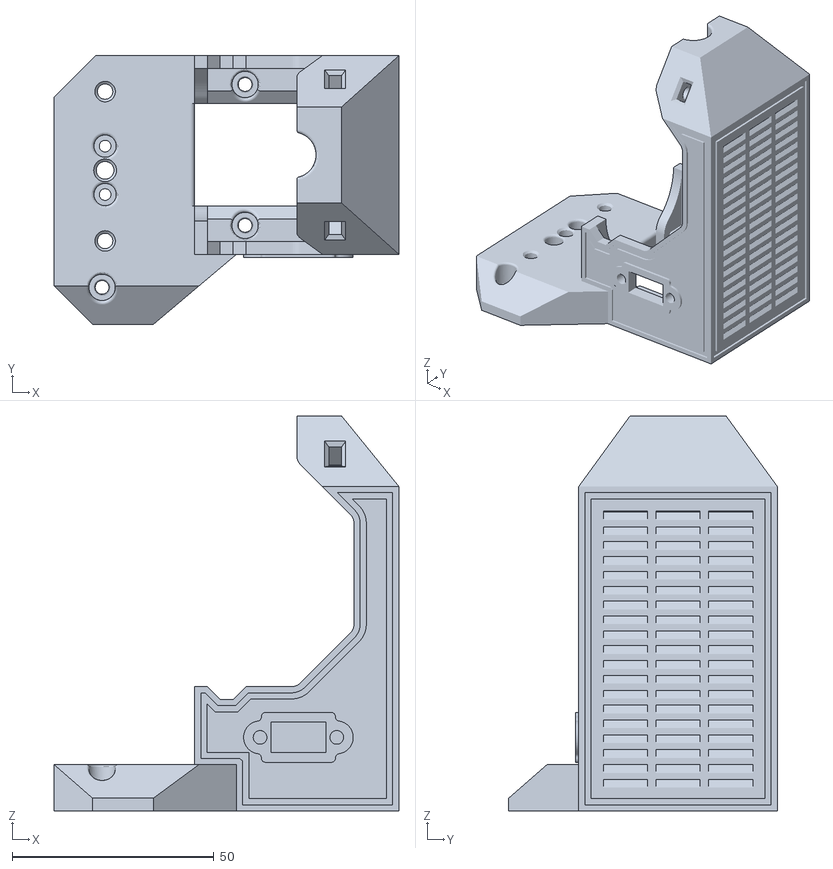
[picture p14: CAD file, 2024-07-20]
3D Models/Orbiter V2/MULDEX-50-02.stl
85.4 x 66.6 x 97.9

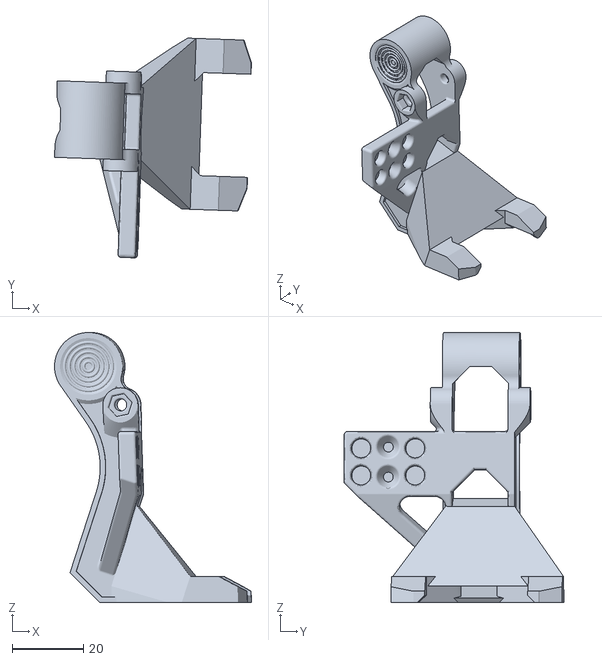
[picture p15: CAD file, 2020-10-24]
3D Models/BMG/MULDEX-39-04.stl
55.3 x 61.7 x 75.8

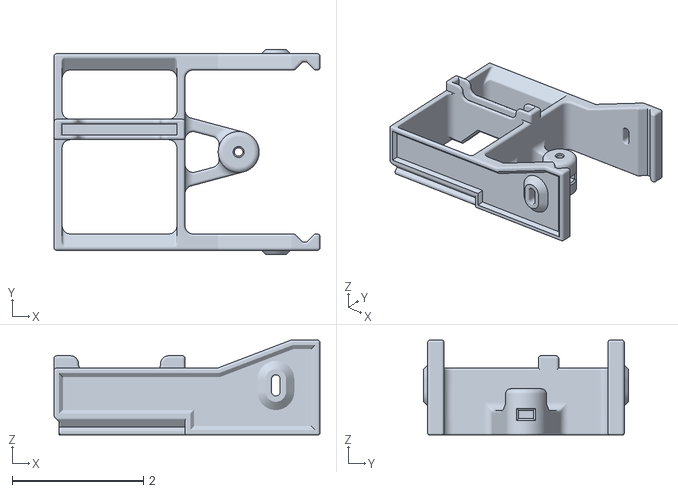
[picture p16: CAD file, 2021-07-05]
3D Models/MULDEX-34-01.stl
4.06 x 3.13 x 1.45

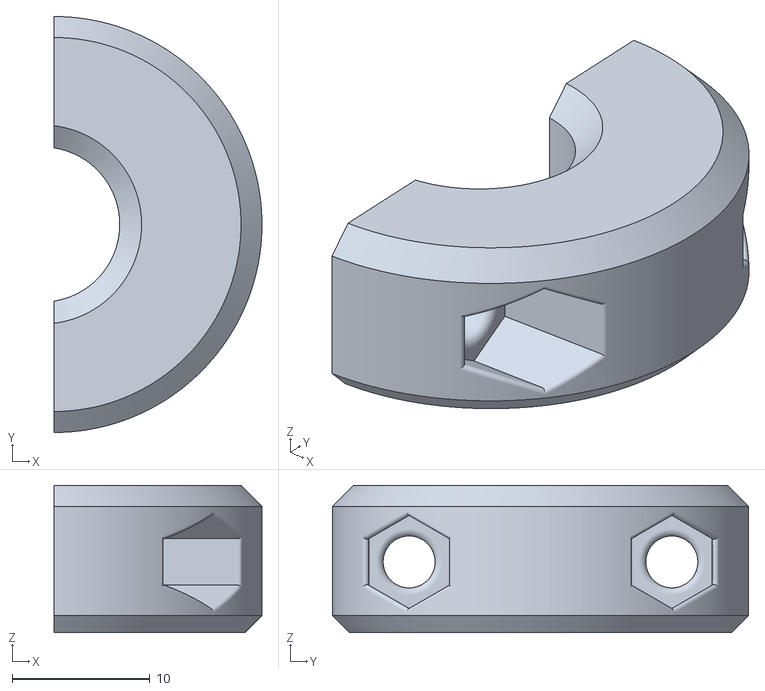
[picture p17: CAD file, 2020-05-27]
3D Models/Nimble/MULDEX-12-07.stl
15.1 x 30.2 x 10.7

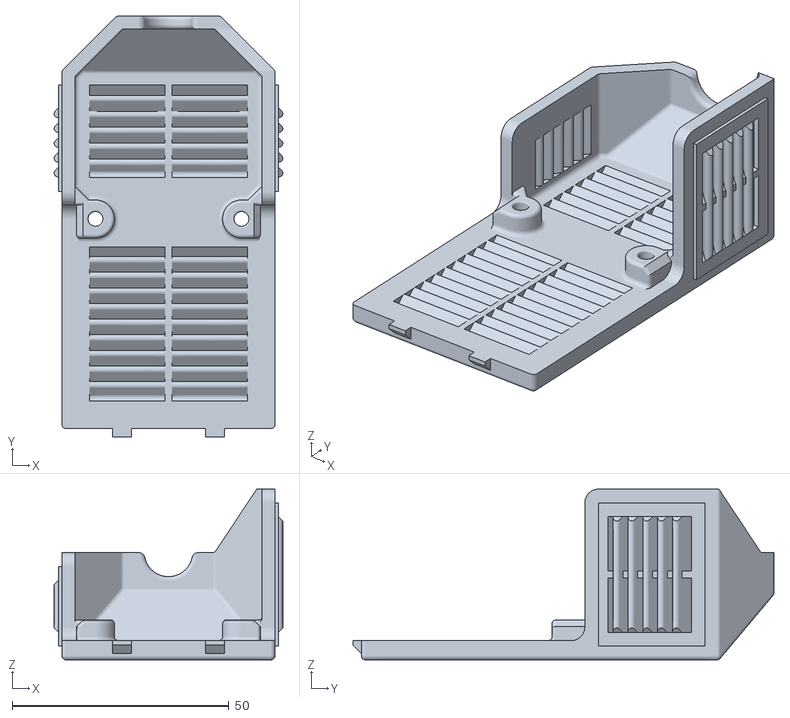
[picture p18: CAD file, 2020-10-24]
3D Models/BMG/MULDEX-40-03.stl
52.8 x 97.2 x 39.4

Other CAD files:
Detailed Drawings/DL1/DL1_MULDEX-03-03.dwg
3D Models/BMG/MULDEX-40-05.stl
Detailed Drawings/DL1/DL1_MULDEX-01-09.dwg
3D Models/Orbiter V2/MULDEX-50-03.stl
Detailed Drawings/DL1/DL1_MULDEX-19-03.dwg
3D Models/BMG/MULDEX-39-03.stl
3D Models/BMG/MULDEX-40-01.stl
3D Models/BMG/MULDEX-40-04.stl
3D Models/MULDEX-01-01.stl
3D Models/MULDEX-01-02.stl
3D Models/MULDEX-01-03.stl
3D Models/MULDEX-01-04.stl
3D Models/MULDEX-01-05.stl
3D Models/MULDEX-01-06.stl
3D Models/MULDEX-01-07.stl
3D Models/MULDEX-03-01.stl
3D Models/MULDEX-03-02.stl
3D Models/MULDEX-03-04.stl
3D Models/MULDEX-03-05.stl
3D Models/MULDEX-03-06.stl
3D Models/MULDEX-03-07.stl
3D Models/MULDEX-03-08.stl
3D Models/MULDEX-03-09.stl
3D Models/MULDEX-03-10.stl
3D Models/MULDEX-03-11.stl
3D Models/MULDEX-03-12.stl
3D Models/MULDEX-03-13.stl
3D Models/MULDEX-04-01.stl
3D Models/MULDEX-05-01.stl
3D Models/MULDEX-06-01.stl
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

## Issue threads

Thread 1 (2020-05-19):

Suggestion for ABS

ModMike, 2020-05-19:
I love the design and can't wait to build one. I hope it's not presumptuous of me to make a suggest a suggestion.

Could you modify the design to mount the electronics outside the build chamber and plan for a fully enclosed system to allow for a heated chamber?

I guess the electronics could be sealed off but I think it might be cleaner to mount them outside the build chamber. I would also like to avoid having to build a hat to enclose the machine.

It's nice to see a design from a real engineer!

sorren4, 2020-05-19:
I would imagine that you could use most/all of the same mount points for the electronics, etc. internally but mount them to the other side of the same panel holes.  I know that's a technical possibility with my Railcore as long as I didn't want to use the same panels on the inside as I have around the electronics on the outside.

3dprintingworld, 2020-05-20:
The frame could definitely be extended to enclose the chamber.  Since I built it for MRRF I wanted it to be open so people can see the belt kinematics easier so I did not enclose it.  My thought was that the motors and electronics would stay where they are but I would extend the wall all the way up between them.

ModMike, 2020-05-20:
The Muldex screams ABS :-)

3dprintingworld, 2020-05-20:
> The Muldex screams ABS :-)

I agree, with all the motors stationary mounted behind the frame would make it perfect.

Closed 2021-03-21.

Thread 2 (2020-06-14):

stepper mounts issue

elk0, 2020-06-14:
We may have 2 issues with the STL files 22-01 and 23-01:
 - These numbers refer to the U and X axis stepper mounts in the drawings, however they seem to carry the motor higher than the other stepper mounts (24-01 & 25-01), so I believe these are the Y axis mounts.
 - The "groove" aimed to center the stepper motor is 20.2mm wide instead of 22mm in the Nema 17 standard so the motors don't fit. See attached pictures.

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

3dprintingworld, 2020-06-15:
Sorry about that, I remember it now. I forgot to update the design because I never reprinted it and was able to open the parts up with a exacto knife to make it work. I have updated the files for the correct pilot diameter now.

elk0, 2020-06-15:
Hi John; thanks for the info and for correcting the files.
The online files aren't updated yet.
Do you mean you will update it later?

3dprintingworld, 2020-06-15:
Sorry I'm not good with github, I forgot to push the changes or something.... It should be updated now.  If not, let me know.

elk0, 2020-06-15:
I don't know these GIT things at all so I won't blame you!
That looks way better now, thank you!

Closed 2020-06-15.

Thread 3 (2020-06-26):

Missing STLs

elk0, 2020-06-26:
I listed the following STLs that are represented in the assembly drawings but currently missing in the GitHub repository.

MULDEX-29-01 REVERSE BOWDEN BRACKET
MULDEX-29-02 EXTRUDER CABLE, RELIF
MULDEX-29-03 EXTRUDER CABLE, CLAMP
MULDEX-29-04 WIRE COMB, FRONT
MULDEX-29-05 WIRE COMB, BACK

MULDEX-33-01 SCRAPPER, FRAME
MULDEX-33-02 PURGE BIN
MULDEX-33-03 SCRAPPER BASE
MULDEX-33-04 SCRAPER KNOB
MULBOT-34 SCRAPPER, FRAME X-AXIS

MULDEX-36-xx LIGHT END BRACKET, RH
MULDEX-36-02 LIGHT END BRACKET, LH

MULDEX-37-01 Y-AXIS SWITCH BRACKET
MULDEX-38 SWITCH BRACKET, LH

3dprintingworld, 2020-06-27:
Thanks for finding the missing files, I also fixed the typos. Let me know if you find anymore missing files.

FYI... The purge buckets assemblies 33 and 34 have not been tested yet. I revised the design from a earlier version but went with the ooze shield instead.

elk0, 2020-06-27:
Thanks a lot for uploading the files.
Just to let you know, files 07-01 and 34-01 are named MULBOT instead of MULDEX ;-)

3dprintingworld, 2020-06-27:
Force of habit...  I already updated the assembly's but forgot the stl's.

Closed 2020-06-27.

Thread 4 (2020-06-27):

U axis carriage set screws placement

elk0, 2020-06-27:
The set screws of the  axis carriage end up being too short.
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

3dprintingworld, 2020-06-27:
I moved the nut trap on "MULDEX-13-01" to work with the set screw specified in the materials.

I would not say these set screws are necessary.  The idea is that it squares up the carriage to the bearings as well as removes the slop from the bolt holes which will keep them from loosening.  The down side I noticed if tightened too hard it can cause the carriage to deform.

elk0, 2020-06-27:
I agree with you and won't re-print this part, but thanks for the next persons building it!
These set screws are one of many details that make this design feel very qualitative and professional.

3dprintingworld, 2020-06-27:
Using the set screws to square up the blocks is very common in machine design and I was supersized no one was doing it on 3D printers. The only extra cost being the setscrews, I thought it worth incorporating into the design.

Closed 2020-06-27.

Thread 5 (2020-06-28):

X-axis carriage cover screw holes not blinded

elk0, 2020-06-28:
I noticed that the screw holes that would normally require supports are generally blinded to prevent the support need, but the one in part MULDEX-12-05 / X-AXIS CARRIAGE COVER aren't.
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

3dprintingworld, 2020-06-28:
I had the end of part rolled back and didn't realize it.  Fixed now!

elk0, 2020-06-28:
Quick and perfect, thank you!

Closed 2020-06-28.

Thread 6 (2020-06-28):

missing STLs

elk0, 2020-06-28:
The following STLs are listed in the BOM (thanks for releasing it), but not in the STLs on GitHub:
MULDEX-01-03 / PANNEL SUPPORT
MULDEX-03-04 / DUET SPACER
MULDEX-03-08 / WIRE CLIP

3dprintingworld, 2020-06-29:
I just added them!

08 was just something I made to keep the wires trapped in the extrusions.  There might be something better already designed on thingiverse, but these seem to work pretty good.

elk0, 2020-06-29:
Thanks again!
That was probably the last missing STLs.

Closed 2020-06-29.

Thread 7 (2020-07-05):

Typo in config.g?

elk0, 2020-07-05:
I spotted this in config.g:

_; Drives
M569 P1 S0                                      ; X physical drive 0 goes backwards
M569 P1 S1                                      ; Y right physical drive 1 goes forwards_

Both lines refer to P1 driver.
The first line should probably refer to P0.
I guess that might have an impact on further X/Y functions.

3dprintingworld, 2020-07-05:
Oh, wow!  Thanks for pointing this out.

3dprintingworld, 2020-07-05:
Strange that the typo did not seem to have any impact, I assume it must of defaulted to a direction when not specified.

elk0, 2020-07-06:
Fine then, I close the issue

Closed 2020-07-06.

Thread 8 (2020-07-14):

Auto level configuration

elk0, 2020-07-14:
In config.g you have

> M671 X-20.6:200:420.6 Y14.3:333.3:14.3 S2       ; Locations left, center, right

defining the Z axis locations for the auto leveling process

In bed.g you have

> G30 P0 X200 Y285 Z-99999   ; Probe Middle
> G30 P1 X65 Y15 Z-99999     ; Probe Left
> G30 P2 X385 Y15 Z-99999 S3 ; Probe Right

I read in https://betrue3d.dk/bltouch-on-duet-wifi-configuratio-and-usage/ that the G30 sequence should be the same as in the M671 config. Here it's not.
My G32 command (auto level) wasn't working until I fixed this by putting the "Left" G30 command first in bed.g.

3dprintingworld, 2020-07-14:
Strange, It appears to be working properly on my end.  I do still have some height issues but I thought that has something to do with mesh bed leveling not working right, or bubbles under my Buildtak.  I'll change it, at the very least it will be cleaner.

DC did state this to me on a previous conversation on the Duet forum when I was originally had issues with this feature; "The probe order doesn't matter. But the order of the leadscrew coordinates in the M671 command must match the order of the corresponding motor drivers in the M584 command. No need to change your wiring, just correct one of those commands to match the other."  According to this the order should not matter but he could be wrong.  I'll give it a try tonight, thanks for noting it.

elk0, 2020-07-14:
You must be right. I think I made other changes at the same time. I probably had something else wrong.

3dprintingworld, 2020-07-14:
Either way, thanks for pointing it out.  I appreciate your help!  Im excited to see what else you find.

Closed 2020-07-14.

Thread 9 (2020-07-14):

Z-AXIS MOTOR MOUNT 2 dimension issue

elk0, 2020-07-14:
On part "MULDEX-17-04" / "Z-AXIS MOTOR MOUNT, 2" I had issues assembling the geared motor because its screw holes's distance to center were too short. I re-drilled it and didn't properly compare with the other Z axis motor mounts because I had already assembled it, but measuring on the STL files tend to confirm that.
No issue with "MULDEX-16-01" / "Z-AXIS MOTOR MOUNT, 1&3".

3dprintingworld, 2020-07-14:
Oh sorry about that....  LDO made a mistake on one of the gear motors I was provided and put the holes in the wrong spot. I offset the holes in the design so they line up with the incorrect spacing on the box but I forgot to change it back to the standard hole spacing for others.  I'll update it shortly.

3dprintingworld, 2020-07-18:
Ok, all fixed, Changed from the 28mm B.C. to 30mm like it should have been.  I released these last because I knew I needed to update something but it slipped my mind...

elk0, 2020-07-18:
Thanks for that!

elk0, 2020-07-24:
I reprinted this part. It's now a perfect fit.

Closed 2020-07-18.

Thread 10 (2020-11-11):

typo in config.g

elk0, 2020-11-11:
Hi
Line 68 of config.g currently is
M307 H2 B0 S1.01
Whether the S parameter of M307 should be between 0 and 1.
I believe it was meant to be
M307 H2 B0 S1.00

3dprintingworld, 2020-11-11:
Thanks!  Fixed

elk0, 2020-11-11:
Thank you too ;-)
I close this issue

Closed 2020-11-11.

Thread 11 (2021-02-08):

Bed and panel files?

ricsmo, 2021-02-08:
Maybe I missed them, but I didn't see files for the bed and panels.

I'm currently building a Mulbot and an [MPCNC](https://www.v1engineering.com/specifications/) and would love for the first MPCNC project to be milling the bed and panels for the Muldex.

Will these files be available upon release or does this have to do with sponsorship in any way?

3dprintingworld, 2021-02-08:
That sounds like a awesome project!  The files you are looking for are available, see link below. They are 2D detail drawings, if you need a model you can pull it from the step file.  I'll work on changing the titles so they don't say "pre-release" as they have not changed.

https://github.com/3dprintingworld/MULDEX/tree/master/Detailed%20Drawings

ricsmo, 2021-02-08:
Great. I'm going a bit overboard with building so many things like this lately. I also have a [Ciclop](https://github.com/bqlabs/ciclop) and [Dremel CNC](https://www.thingiverse.com/thing:3004773) that I'm halfway done with so I'll wait until the official release because I have time plus I have to figure out where to put all the new machines :). I found the Muldex looking for Mulbot stuff and was immediately excited. Can't wait for the release. I was going to build [this](https://docs.v1engineering.com/mp3dp/) from the same maker as the MPCNC, but since my main printer is a heavily modified Ender 3 (Duet 2, linear rails, etc.) and I'm building the Mulbot, the Muldex is unlike anything else I'd have so it gets priority. Thanks so much for making these and making them open source. I'm not great at anything CAD yet (even struggle at cutting stl models into 2 pieces to be honest), but since this seems like it's becoming an addition hobby I'll eventually learn and be able to contribute with remixes, addons, etc.  At the minimum maybe I'll publish any customizations I make to my firmware.

3dprintingworld, 2021-02-12:
Glad you like the design, I really like it to! It didn't happen like I thought it would but I would consider it released.  Drawing are final, I just need to change the names. If you are considering building one, LDO made a short run of kits you might be interested in.  Links for the kits are in the readme.

It would be awesome if you want to contribute! I'm exited to hear everyone's feedback and idea's so we can make it even better than it already is. If its mechanical or firmware tweak I'm all ears. We also have a facebook group if your interested in that discussion.

3dprintingworld, 2021-03-07:
I have updated all the draws so they no longer say "preliminary".

Closed 2021-03-07.

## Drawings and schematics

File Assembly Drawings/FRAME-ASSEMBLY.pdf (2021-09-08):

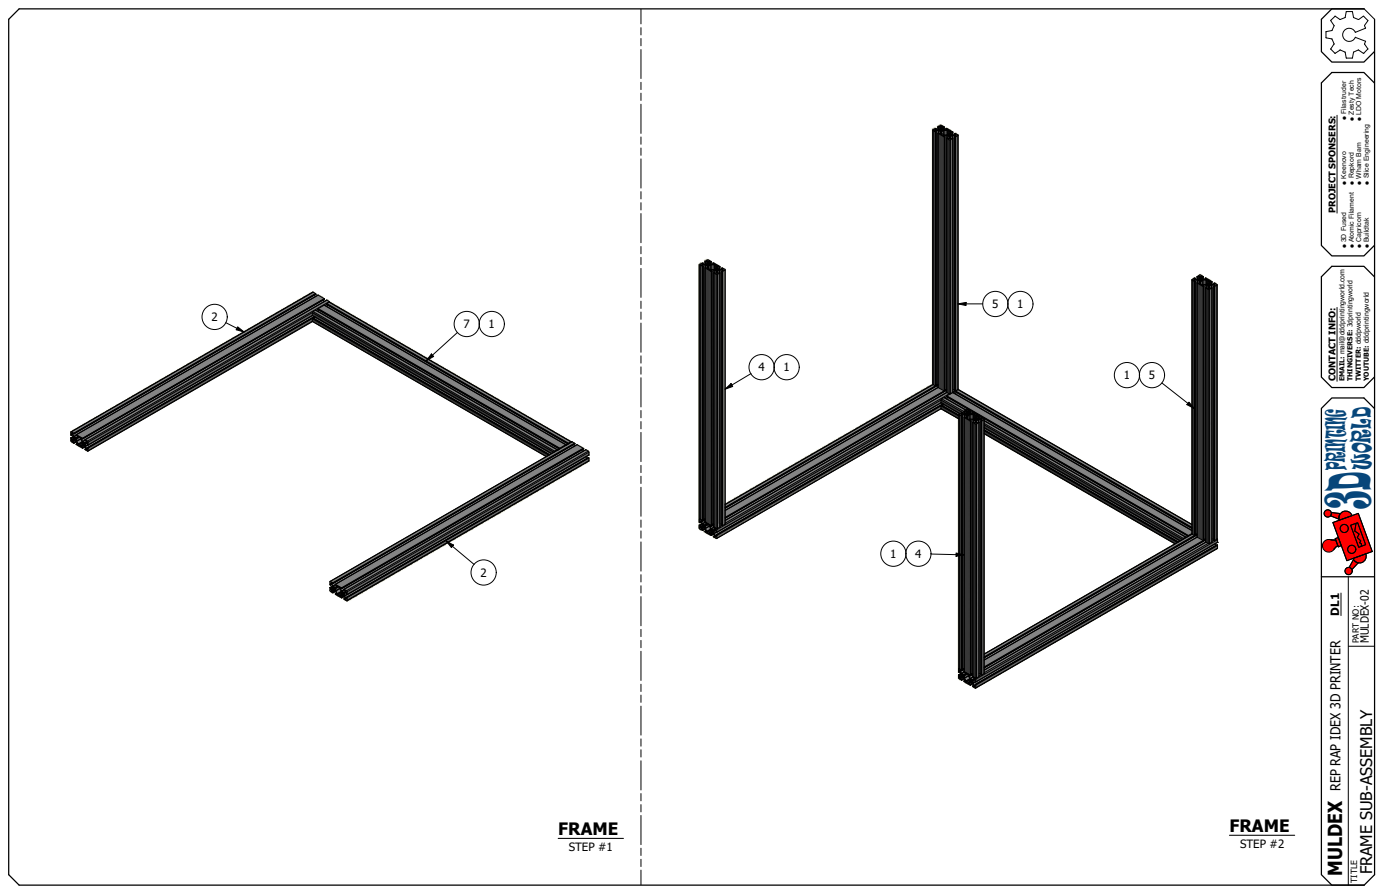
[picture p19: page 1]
PART NO:

MULDEX 3DPRINTING WORLD CONTACT INFO: EMAIL: mail@dddprintingworld.com THINGIVERSE: 3dprintingworld TWITTER: dddpworld YOUTUBE: dddprintingworld  3D Fused  Keenovo  Filastruder  Atomic Filament  Repkord  Zesty Tech  Capricorn  Wham Bam  LDO Motors  Buildtak  Slice Engineering DL1 PROJECT SPONSERS: REP RAP IDEX 3D PRINTER

FRAME SUB-ASSEMBLY

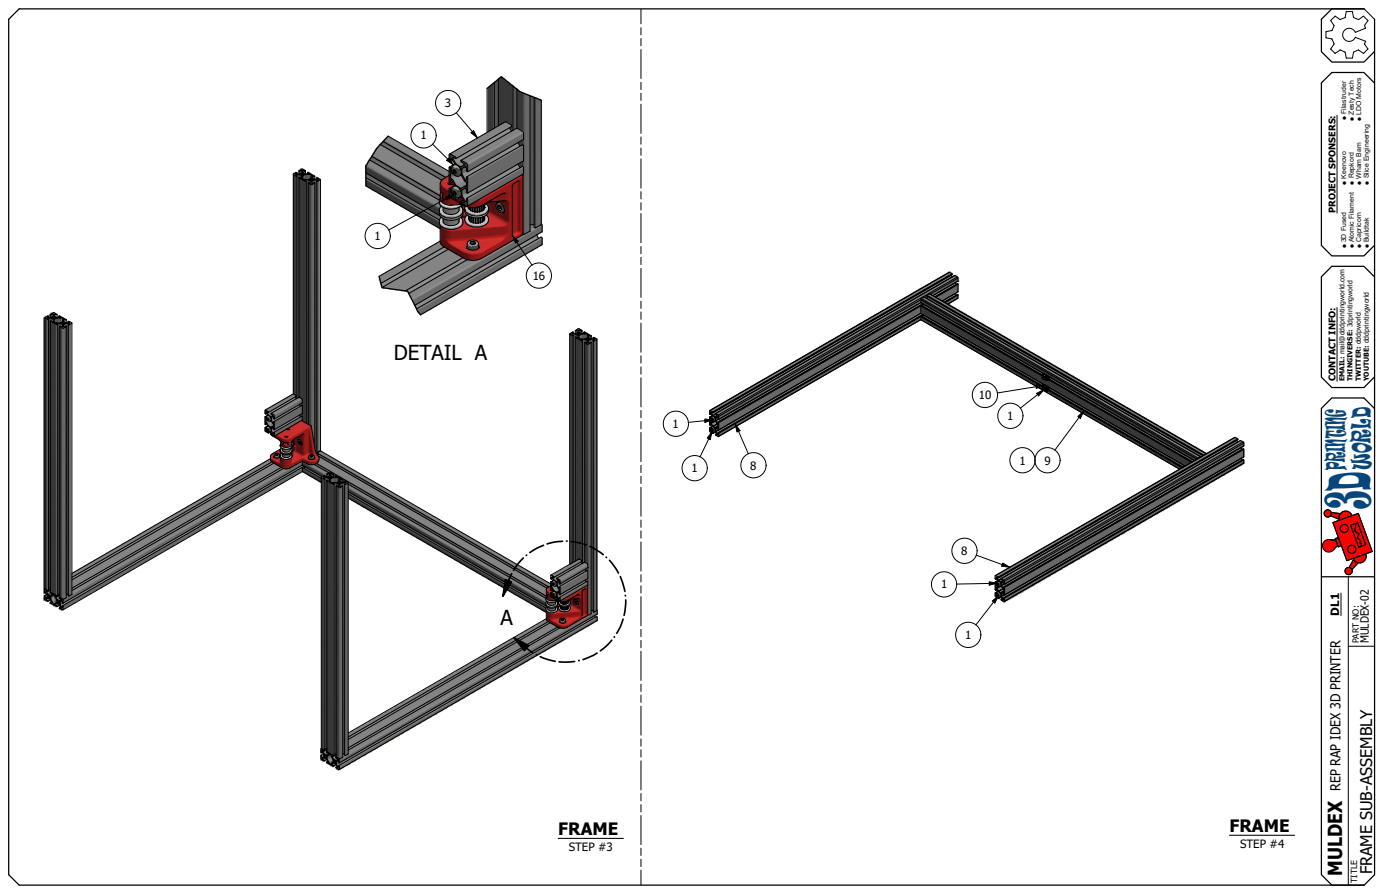
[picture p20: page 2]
PART NO:

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

FRAME SUB-ASSEMBLY

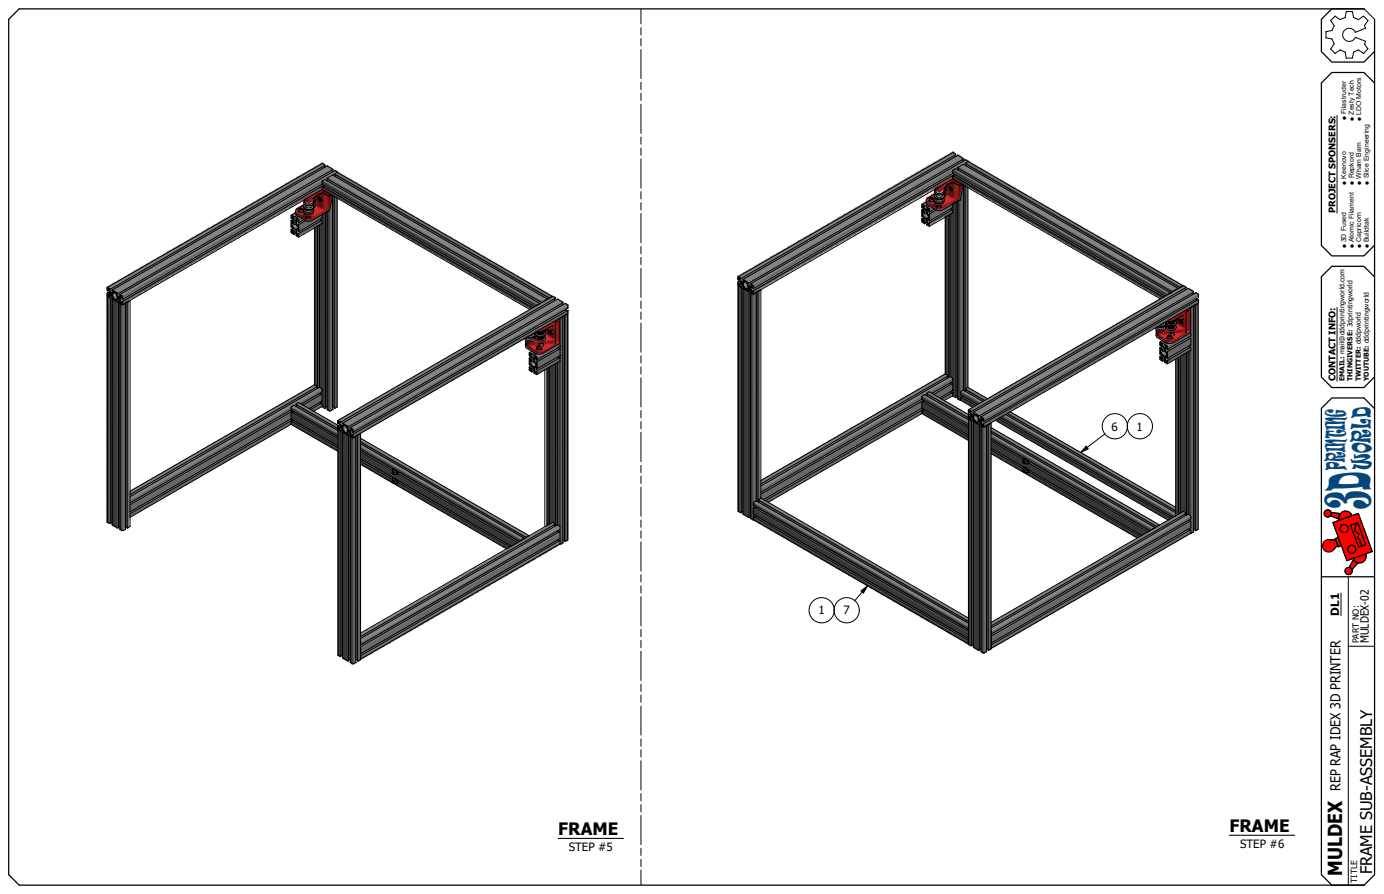
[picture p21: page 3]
PART NO:

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

FRAME SUB-ASSEMBLY

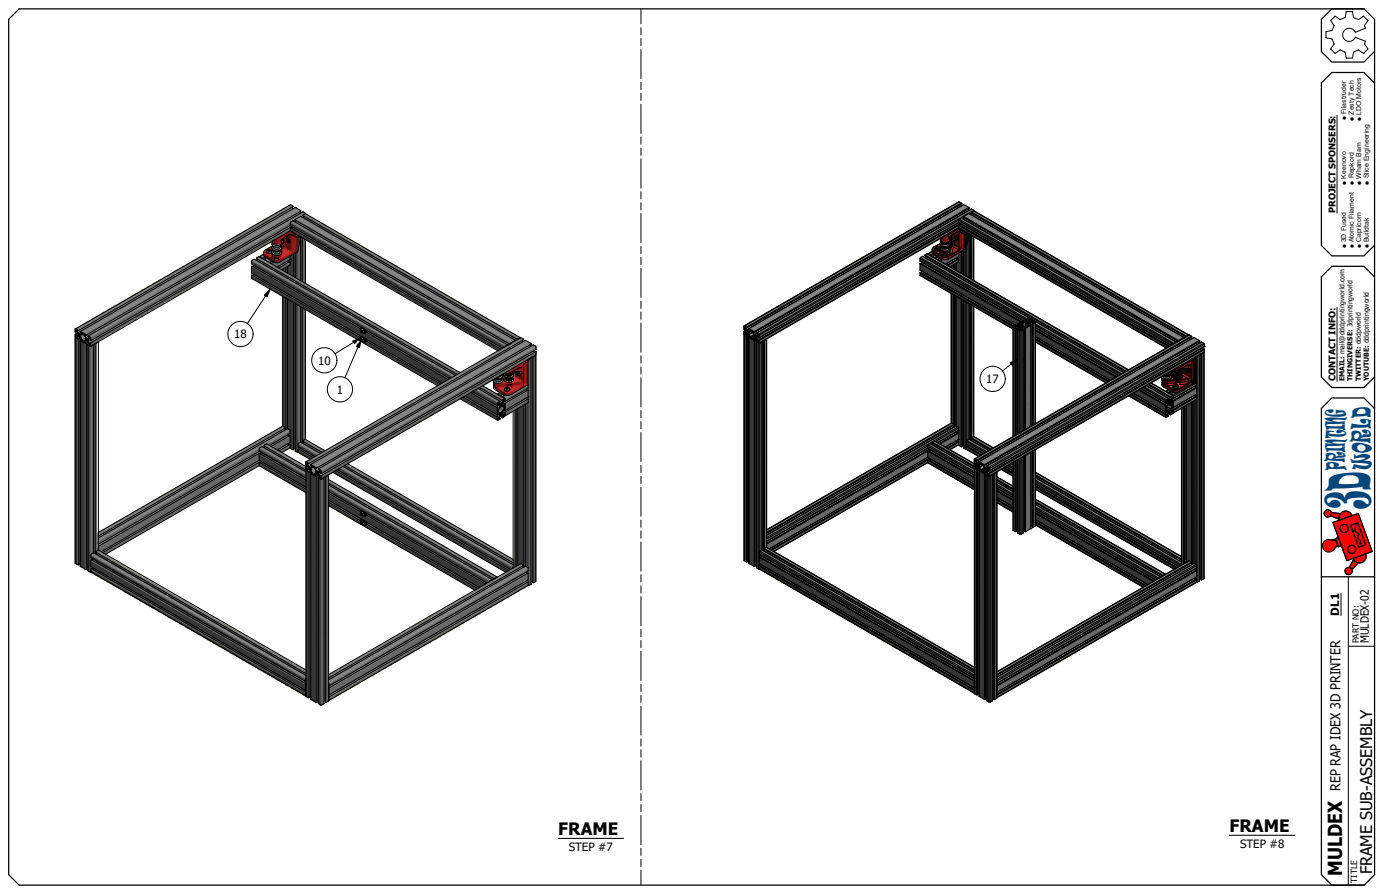
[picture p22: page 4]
PART NO:

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

FRAME SUB-ASSEMBLY

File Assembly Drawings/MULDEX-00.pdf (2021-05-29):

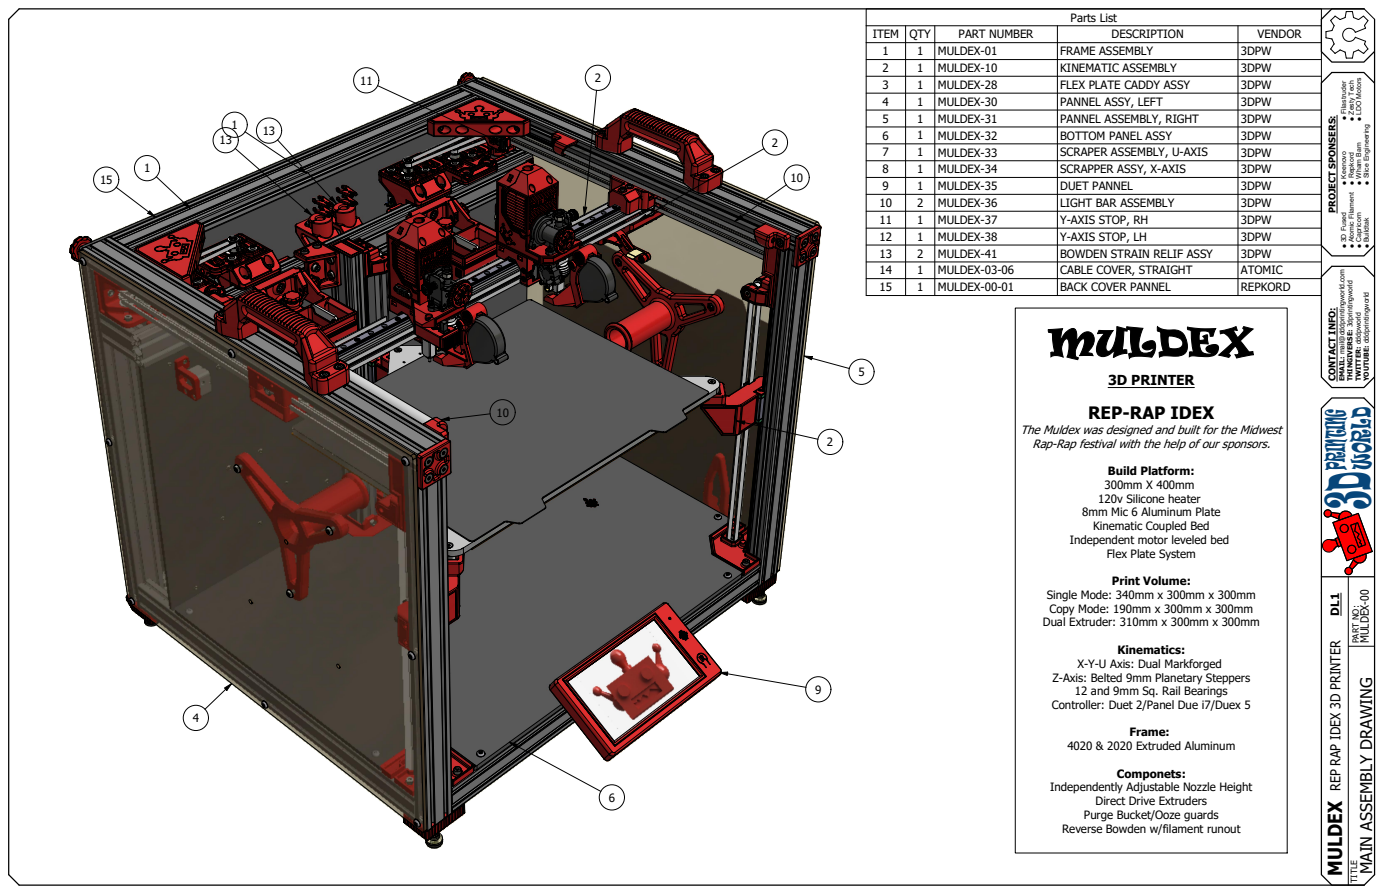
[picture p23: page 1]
PART NO:

MULDEX 3DPRINTING WORLD CONTACT INFO: EMAIL: mail@dddprintingworld.com THINGIVERSE: 3dprintingworld TWITTER: dddpworld YOUTUBE: dddprintingworld  3D Fused  Keenovo  Filastruder  Atomic Filament  Repkord  Zesty Tech  Capricorn  Wham Bam  LDO Motors  Buildtak  Slice Engineering DL1 PROJECT SPONSERS: REP RAP IDEX 3D PRINTER

MAIN ASSEMBLY DRAWING

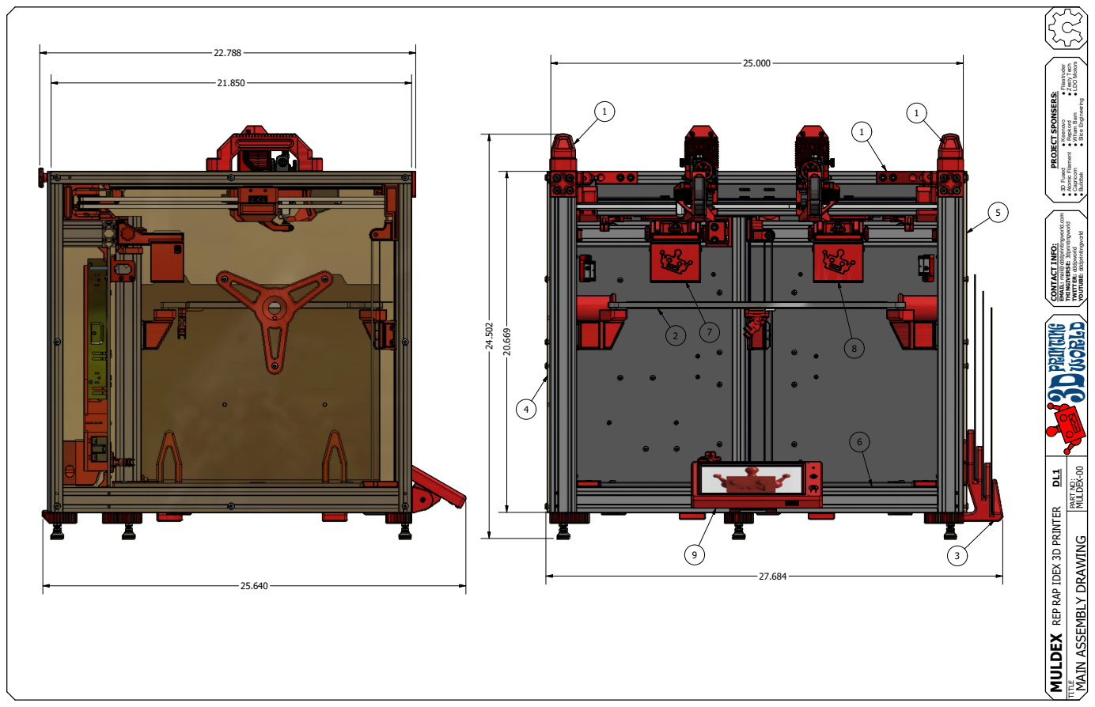
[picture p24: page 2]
PART NO:

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

MAIN ASSEMBLY DRAWING

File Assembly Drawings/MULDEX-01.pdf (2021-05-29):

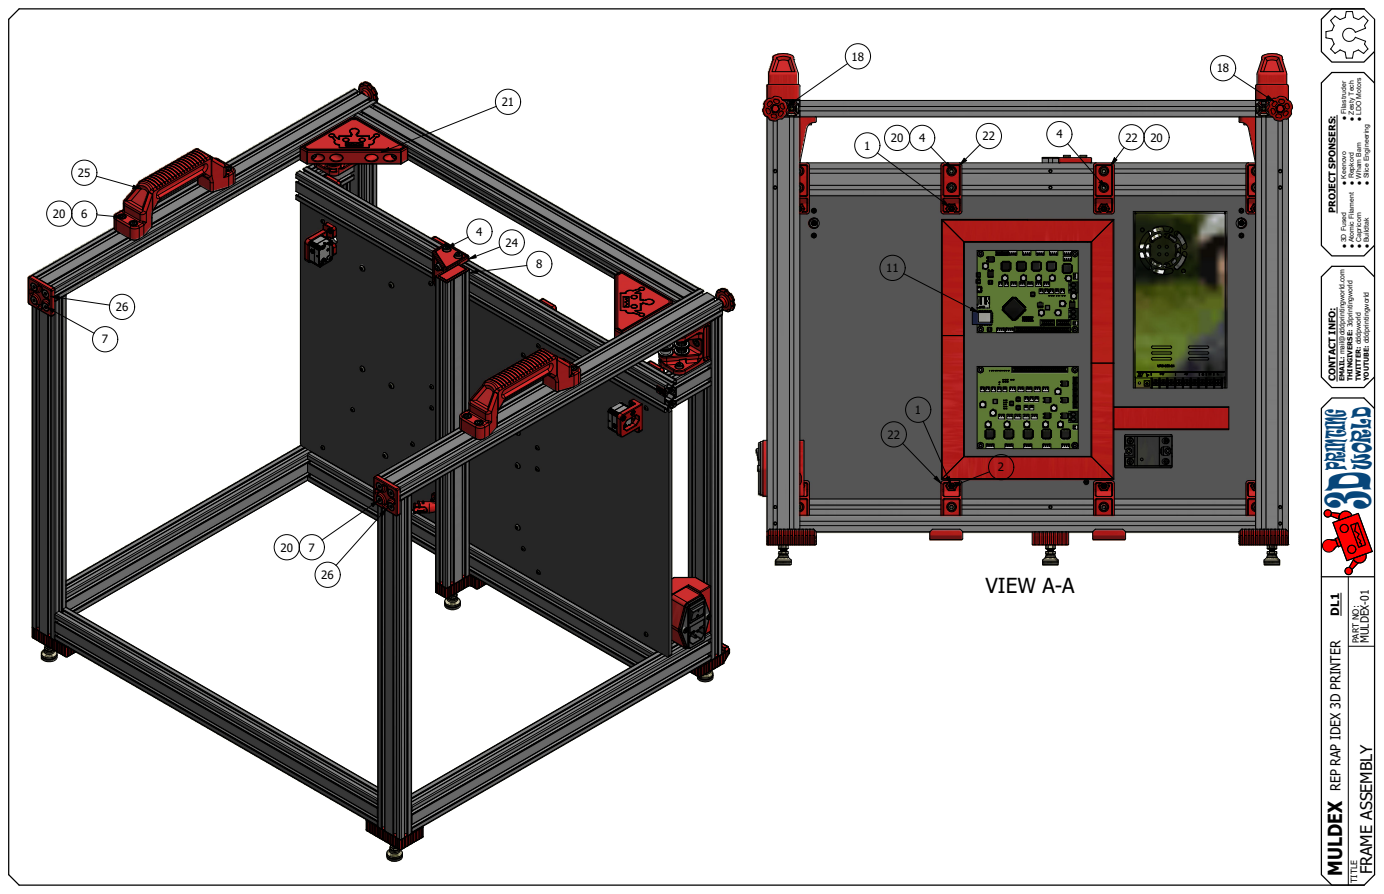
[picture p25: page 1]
PART NO:; FRAME ASSEMBLY

MULDEX 3DPRINTING WORLD CONTACT INFO: EMAIL: mail@dddprintingworld.com THINGIVERSE: 3dprintingworld TWITTER: dddpworld YOUTUBE: dddprintingworld  3D Fused  Keenovo  Filastruder  Atomic Filament  Repkord  Zesty Tech  Capricorn  Wham Bam  LDO Motors  Buildtak  Slice Engineering DL1 PROJECT SPONSERS: REP RAP IDEX 3D PRINTER

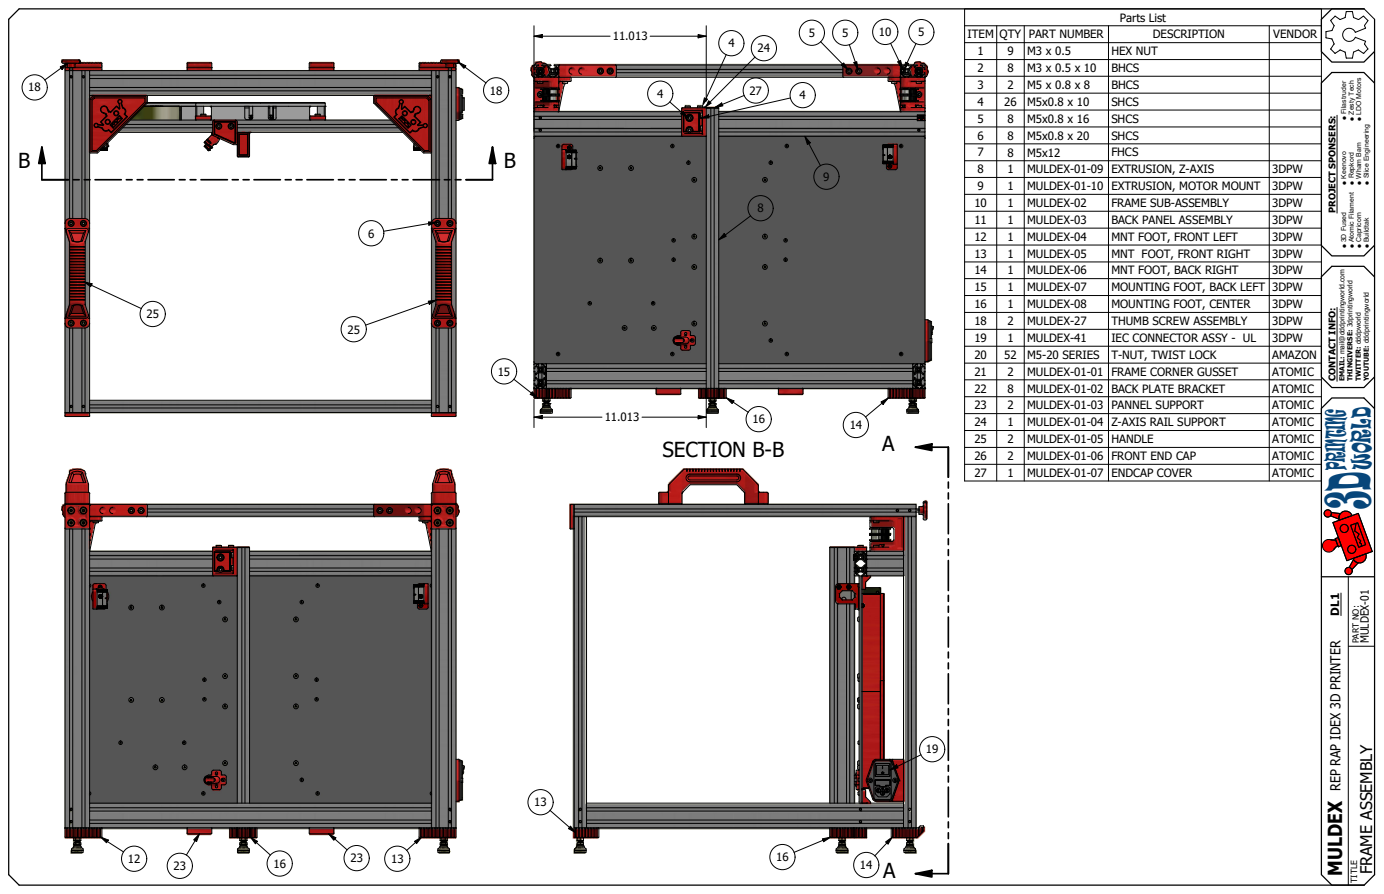
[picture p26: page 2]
PART NO:; FRAME ASSEMBLY

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

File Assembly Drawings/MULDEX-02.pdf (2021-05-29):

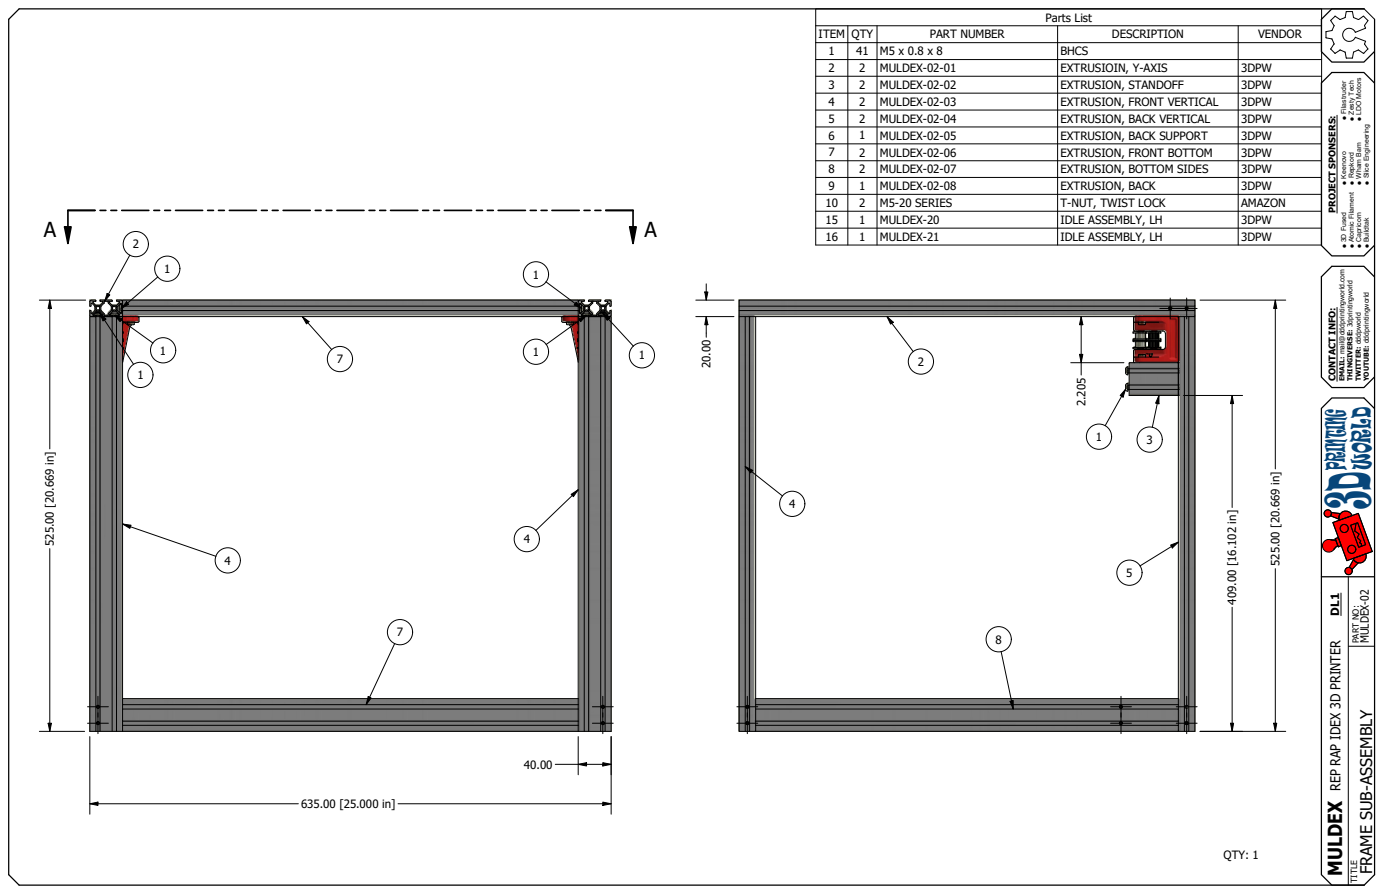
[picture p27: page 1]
PART NO:

I T E M | Q TY | P A RT N U M B E R | D E S C R I P T I O N | V E N D O R
1 | 4 1 | M 5 x 0 . 8 x 8 | B H C S
2 | 2 | M U L D E X -0 2 -0 1 | E X T R U S I O I N , Y -AX I S | 3 D P W
3 | 2 | M U L D E X -0 2 -0 2 | E X T R U S I O N , S TA N D O F F | 3 D P W
4 | 2 | M U L D E X -0 2 -0 3 | E X T R U S I O N , F R O N T V E RT I C A L | 3 D P W
5 | 2 | M U L D E X -0 2 -0 4 | E X T R U S I O N , B A C K V E RT I C A L | 3 D P W
6 | 1 | M U L D E X -0 2 -0 5 | E X T R U S I O N , B A C K S U P P O RT | 3 D P W
7 | 2 | M U L D E X -0 2 -0 6 | E X T R U S I O N , F R O N T B O TT O M | 3 D P W
8 | 2 | M U L D E X -0 2 -0 7 | E X T R U S I O N , B O TT O M S I D E S | 3 D P W
9 | 1 | M U L D E X -0 2 -0 8 | E X T R U S I O N , B A C K | 3 D P W
1 0 | 2 | M 5 -2 0 S E R I E S | T -N U T , T W I S T L O C K | A M A Z O N
1 5 | 1 | M U L D E X -2 0 | I D L E A S S E M B LY , L H | 3 D P W
1 6 | 1 | M U L D E X -2 1 | I D L E A S S E M B LY , L H | 3 D P W

MULDEX 3DPRINTING WORLD CONTACT INFO: EMAIL: mail@dddprintingworld.com THINGIVERSE: 3dprintingworld TWITTER: dddpworld YOUTUBE: dddprintingworld  3D Fused  Keenovo  Filastruder  Atomic Filament  Repkord  Zesty Tech  Capricorn  Wham Bam  LDO Motors  Buildtak  Slice Engineering DL1 PROJECT SPONSERS: REP RAP IDEX 3D PRINTER

FRAME SUB-ASSEMBLY

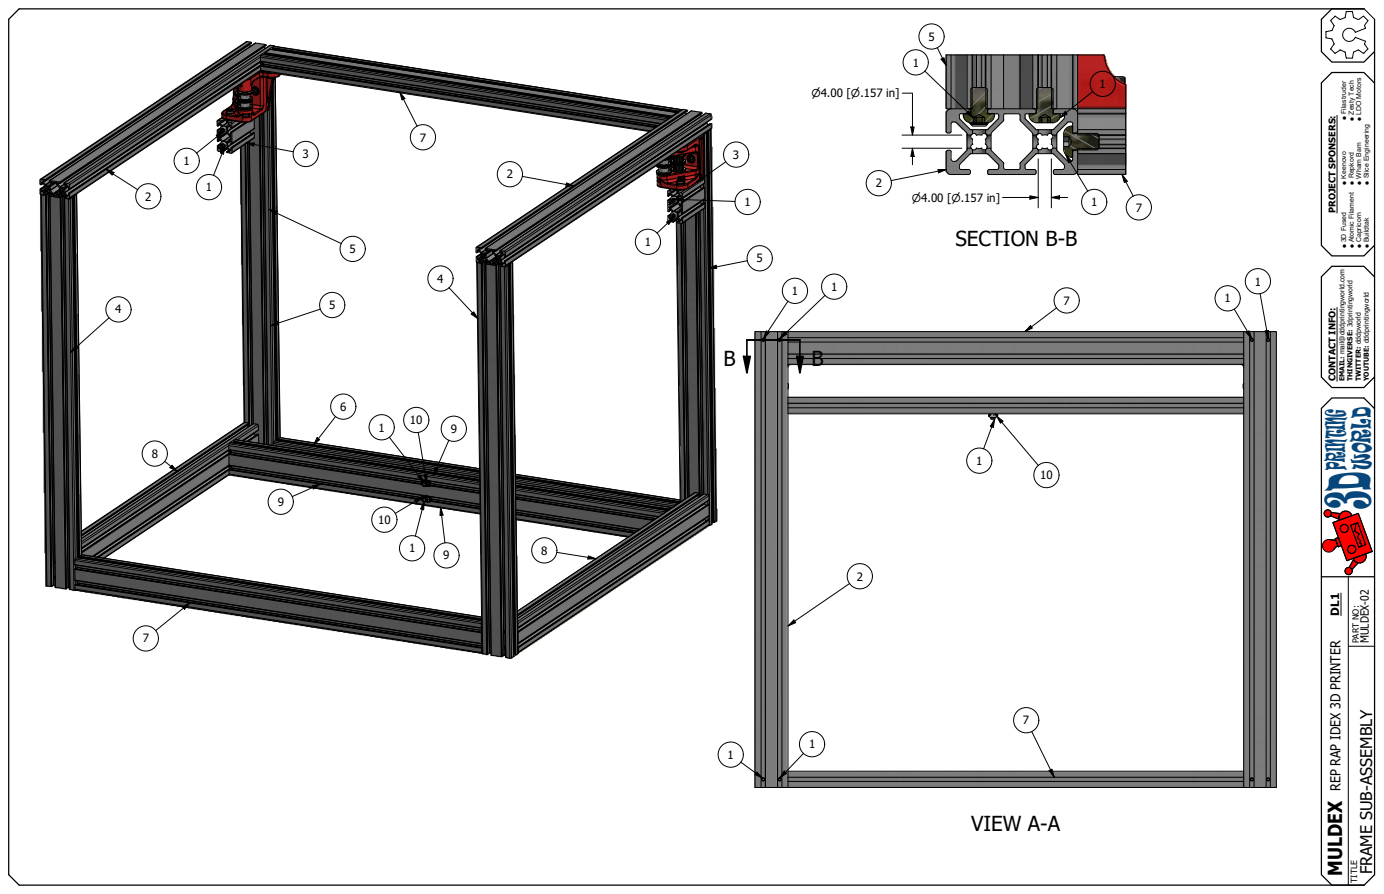
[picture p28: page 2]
PART NO:

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

FRAME SUB-ASSEMBLY

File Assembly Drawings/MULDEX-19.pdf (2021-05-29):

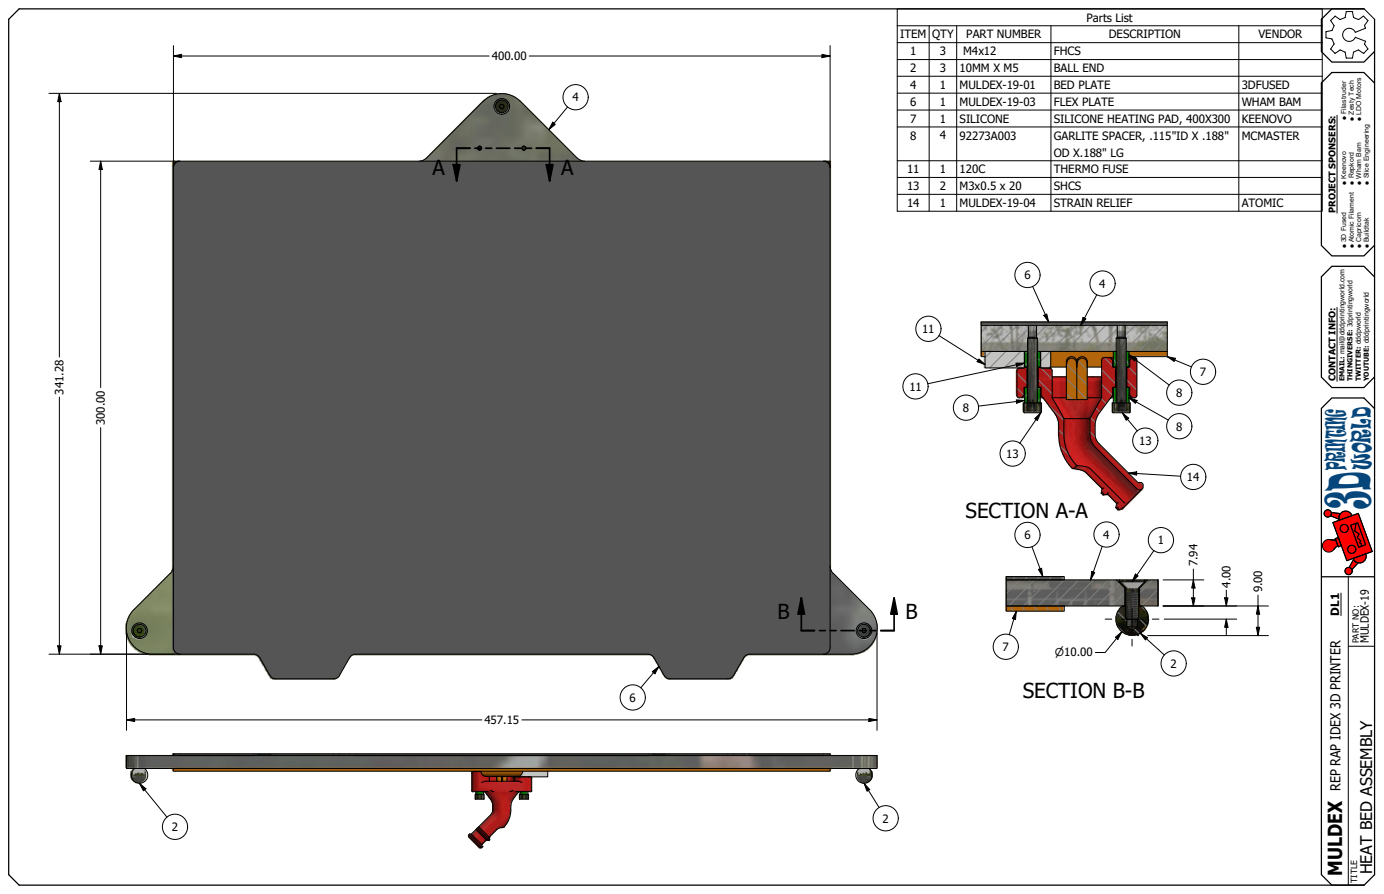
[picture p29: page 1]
PART NO:

I T E M | Q T Y | P A RT N U M B E R | D E S C R I P T I O N | V E N D O R
1 | 3 | M 4 x 1 2 | F H C S
2 | 3 | 1 0 M M X M 5 | B A L L E N D
4 | 1 | M U L D E X -1 9 -0 1 | B E D P LAT E | 3 D F U S E D
6 | 1 | M U L D E X -1 9 -0 3 | F L E X P L AT E | W H A M B A M
7 | 1 | S I L I C O N E | S I L I C O N E H E AT I N G P A D , 4 0 0 X 3 0 0 | K E E N O V O
8 | 4 | 9 2 2 7 3 A 0 0 3 | G A R L I T E S P A C E R , . 1 1 5 " I D X . 1 8 8 " O D X . 1 8 8 " L G | M C M A S T E R

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

1 1 | 1 | 1 2 0 C | T H E R M O F U S E
1 3 | 2 | M 3 x 0 . 5 x 2 0 | S H C S
1 4 | 1 | M U L D E X -1 9 -0 4 | S T RA I N R E L I E F | AT O M I C

HEAT BED ASSEMBLY

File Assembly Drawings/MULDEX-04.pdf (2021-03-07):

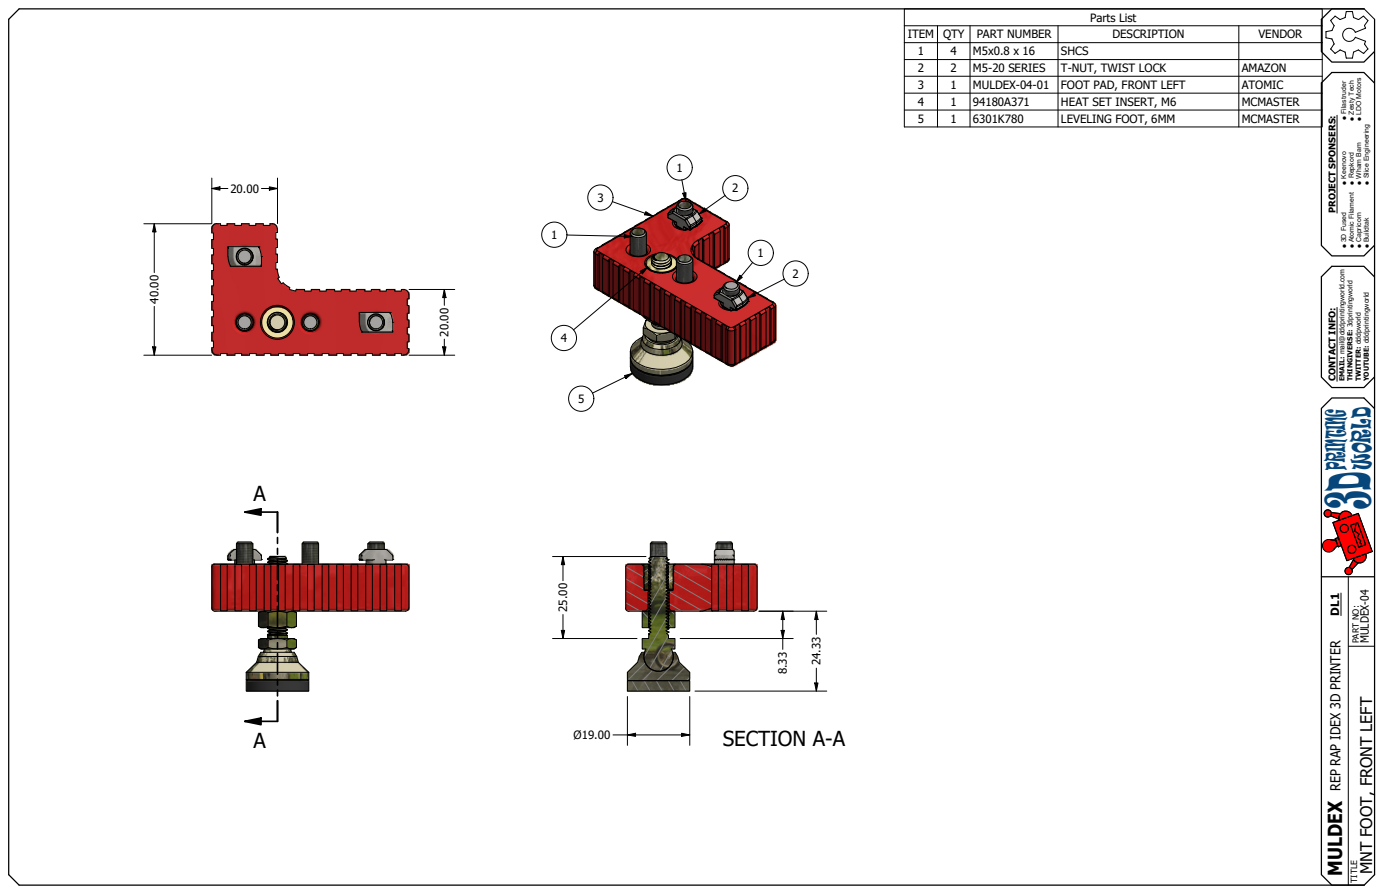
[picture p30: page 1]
PART NO:

I T E M | Q TY | P A RT N U M B E R | D E S C R I P T I O N | V E N D O R
1 | 4 | M 5 x 0 . 8 x 1 6 | S H C S
2 | 2 | M 5 -2 0 S E R I E S | T -N U T , T W I S T L O C K | A M A Z O N
3 | 1 | M U L D E X -0 4 -0 1 | F O O T P A D , F R O N T L E F T | AT O M I C
4 | 1 | 9 4 1 8 0 A 3 7 1 | H E AT S E T I N S E RT , M 6 | M C M A S T E R
5 | 1 | 6 3 0 1 K 7 8 0 | L E V E L I N G F O O T , 6 M M | M C M A S T E R

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

MNT FOOT, FRONT LEFT

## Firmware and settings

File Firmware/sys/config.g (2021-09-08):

G90                                             ; send absolute coordinates...
M83                                             ; ...but relative extruder moves
M550 P"Muldex"                                  ; set printer name


; Network
M552 S1                                         ; enable network
M586 P0 S1                                      ; enable HTTP
M586 P1 S0                                      ; disable FTP
M586 P2 S0                                      ; disable Telnet

; Drives
M569 P0 S1                                      ; X physical drive 0 goes backwards
M569 P1 S1                                      ; Y right physical drive 1 goes forwards
M569 P2 S0                                      ; Y left physical drive 2 goes backwards
M569 P3 S0                                      ; U physical drive 3 goes forwords
M569 P4 S1                                      ; E1 physical drive 4 goes backwords
M569 P5 S0                                      ; Z left physical drive 5 goes backwards
M569 P6 S0                                      ; Z center physical drive 6 goes backwards
M569 P7 S1                                      ; Z right physical drive 7 goes forwards 
M569 P8 S0                                      ; E2 physical drive 8 goes backwords

M584 X0 Y1:2 U3 Z5:6:7 E4:8                     ; set drive mapping

M350 X16 U16 Y16 Z16 E16:16 I1                                      ; configure microstepping with interpolation
M92 X100.00 U100.00 Y100.00 Z1096 E415.00:655.00                    ; set steps per mm (1760nimble)
M566 X1000.00 U1000.00 Y1000.00 Z100.00 E100.00:300.00              ; set maximum instantaneous speed changes (mm/min)(Nimble 40)
M203 X12000.00 U12000.00 Y12000.00 Z2000.00 E4200.00:4200.00        ; set maximum speeds (mm/min)
M201 X800.00 U800.00 Y800.00 Z100.00 E600.00:600.00                 ; set accelerations (mm/s^2)(500)(Nimble 120)
M906 X700 U700 Y700 Z200 E600:600 I30                               ; set motor currents (mA) and motor idle factor in per cent(Nimble 500)
M84 S30                                                             ; Set idle timeout

; Axis Limits
M208 X-21.4 Y0 U33 Z0 S1                       ; set axis min was (-18 BMG)16.7_X-14.4 Y0 U40 Z0 S1
M208 X344 U413.75 Y334 Z300 S0                 ; set axis max Y WAS 339_X350 U422.7 Y334 Z300 S0(u414.75)

M669 K0 Y1:1:0:1				               ; select Markforged Kinematics Y to react with X and U

; Endstops 
M574 X1 S1 P"xstop"                            ; X axis active high endstop switch
M574 Y2 S1 P"ystop+zstop"                      ; Y Double max active high endstop switch
M574 U2 S1 P"duex.e2stop"                      ; U axis active high endstop switch
M574 Z1 S2 					                   ; Define Z to use Probe. Home to Min.

; Filament Sensor
;M591 D0 P3 C"e0stop" S0 R70:130 L24.8 E3.0 ; Duet3D rotating magnet sensor for extruder drive 0 is connected to E0 endstop input, enabled, sensitivity 24.8mm.rev, 70% to 130% tolerance, 3mm detection length
;M591 D1 P3 C"e1stop" S0 R70:130 L24.8 E3.0 ; Duet3D rotating magnet sensor for extruder drive 0 is connected to E0 endstop input, enabled, sensitivity 24.8mm.rev, 70% to 130% tolerance, 3mm detection length

;M591 D0 ; display filament sensor parameters for extruder drive 0
;M591 D1 ; display filament sensor parameters for extruder drive 0

; Z-Probe
M307 H7 A-1 C-1 D-1					            ; Disable the 6th Heater to free up PWM channel 5 on the Duex board.
M671 X-20.6:200:420.6 Y14.3:333.3:14.3 S5       ; Locations left, center, right 
M950 S0 C"duex.e6heat"                          ; create servo pin 0 for BLTouch
M558 P9 C"^zprobe.in" H5 F120 T5000   ; set Z probe type to bltouch and the dive height + speeds 
G31 P25 X-29 Y0 Z1.6                             ; set Z probe trigger value, offset and trigger height(lower number farther away)1.9
M557 X15:360 Y15:290 S20                        ; probe from X=10 to 390, Y=10 to 290mm with a mesh spacing of 20mm S20

; Heaters
M308 S0 P"bedtemp" Y"thermistor" T100000 B4534 C9.565227e-8      ; configure sensor 0 as thermistor on pin bedtemp
M950 H0 C"bedheat" T0                                            ; create bed heater output on bedheat and map it to sensor 0
M143 H0 S120                                                     ; set temperature limit for heater 0 to 120C
M307 H0 B0 S1.00                                                 ; disable bang-bang mode for the bed heater and set PWM limit
M140 H0                                                          ; map heated bed to heater 0
M308 S1 P"e0temp" Y"thermistor" T500000 B4723 C1.196220e-7 R4700 ; configure sensor 1 as thermistor on pin e0temp
M950 H1 C"e0heat" T1                                             ; create nozzle heater output on e0heat and map it to sensor 1
M143 H1 S280                                                     ; set temperature limit for heater 1 to 280C
M307 H1 B0 S1.00                                                 ; disable bang-bang mode for heater  and set PWM limit
M308 S2 P"e1temp" Y"thermistor" T500000 B4723 C1.196220e-7 R4700 ; configure sensor 2 as thermistor on pin e1temp
M950 H2 C"e1heat" T2                                             ; create nozzle heater output on e1heat and map it to sensor 2
M143 H2 S280                                                     ; set temperature limit for heater 2 to 280C
M307 H2 B0 S1.01                                                 ; disable bang-bang mode for heater  and set PWM limit

; Fans
M950 F0 C"fan0" Q500                             ; create fan 0 on pin fan0 and set its frequency
M106 P0 S0 H-1                                   ; set fan 0 value. Thermostatic control is turned off
M950 F1 C"fan1" Q500                             ; create fan 1 on pin fan1 and set its frequency
M106 P1 S1 H1 T45                                ; set fan 1 value. Thermostatic control is turned on
M950 F2 C"fan2" Q500                             ; create fan 2 on pin fan2 and set its frequency
M106 P2 S0 H-1                                   ; set fan 2 value. Thermostatic control is turned off
M950 F3 C"duex.fan8" Q500                        ; create fan 3 on pin duex.fan8 and set its frequency
M106 P3 S1 H2 T45                                ; set fan 3 value. Thermostatic control is turned on

; LEDs
M950 F4 C"duex.fan6" ;Q500                       ; create LED 4 on pin duex.fan6 and set its frequency
M106 P4 S255 H-1                                 ; set LED 4 value. Thermostatic control is turned OFF
M950 F5 C"duex.fan7" ;Q500                       ; create LED 5 on pin duex.fan7 and set its frequency
M106 P5 S255 H-1                                 ; set LED 5 value. Thermostatic control is turned OFF

; Tools
M563 P0 D0 H1 F0 S"Left"                         ; define tool 0 Left 
G10 P0 X0 Y0 Z0                                  ; set tool 0 axis offsets y was .45
G10 P0 R0 S0                                     ; set initial tool 0 active and standby temperatures to 0C

M563 P1 D1 H2 X3 F2 S"Right"                     ; define tool 1 Right
G10 P1 X0 Y0 Z0                              ; set tool 1 axis offsets (.5BMG) (-1.45)
G10 P1 R0 S0                                     ; set initial tool 1 active and standby temperatures to 0C

M563 P2 D0:1 H1:2 X0:3 F0:2 S"Copy"              ; define tool 2 Copy
G10 P2 X90 Y0 U-90 S0 R0                         ; set tool 2 axis offsets (WAS 105)
M567 P2 E1:1         
M568 P2 S1 ; turn on mixing for tool 2           ; set mix ratio 100% on both extruders

M501                                             ; Record

M575 P1 S1 B57600                                ;Panel due 

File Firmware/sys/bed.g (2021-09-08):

if move.axes[2].userPosition < 5	; if Z is too close or not homed
  G1 H2 Z5 F6000    			; then lift Z
M558 F50				; Slow probing speed
G1 F6000                    ; lift Z relative to current position   
G30 P0 X200 Y270 Z-99999   ; Probe Middle
G30 P1 X30 Y30 Z-99999     ; Probe Left G30 P1 X15 Y15 Z-99999 
G30 P2 X310 Y30 Z-99999 S3 ; Probe Right G30 P2 X324 Y15 Z-99999 S3

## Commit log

2020-05-21 DWG's & PDF's
    [PRERELEASE-_MULDEX-00-01.dwg, PRERELEASE-_MULDEX-02-01.dwg, PRERELEASE-_MULDEX-02-02.dwg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]
2020-06-06 prerelease stl
    [MULDEX-16-02.stl, MULDEX-16-03.stl, MULDEX-16-04.stl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]
2020-06-27 updated nut trap
2020-06-28 FIRST RELEASE
    [MULDEX-BOM.xlsx]
2020-07-02 HOLDING POWER
    [STEPPER HOLDING POWER.xlsx]
2020-07-11 dual y-axis endstops
    [bed.g, config.g, homeall.g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]
2020-07-13 SHOULDER DOWELS UPDATE
    [MULDEX-BOM.xlsx]
2020-07-14 Voltage adjustment
    [config.g]
2020-11-11 Fixed bed PMW max typo
    [config.g]
2020-11-18 BMG UPDATE
    [MULDEX-16-02.stl, MULDEX-17-03.stl, MULDEX-18-02.stl]
2021-01-15 UL IEC
    [MULDEX-41-01.stl, MULDEX-41-02.stl]
2021-01-16 INLET SUPPORT
    [MULDEX-03-05.stl]
2021-01-16 Inlet bracket
    [MULDEX-03-05.stl]
2021-03-11 firmware update
    [config.g, homeall.g, homey.g]
2024-07-14 Added mirror of standard
    [Housing 1.5_mirrored.stl, Latch_mirrored.stl]
2024-07-20 Orbiter V2 Carriage Parts
    [MULDEX-50-01.stl, MULDEX-50-02.stl, MULDEX-50-03.stl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]
2024-08-07 updated the panel width
    [DL1_MULDEX-03-03.dwg]
